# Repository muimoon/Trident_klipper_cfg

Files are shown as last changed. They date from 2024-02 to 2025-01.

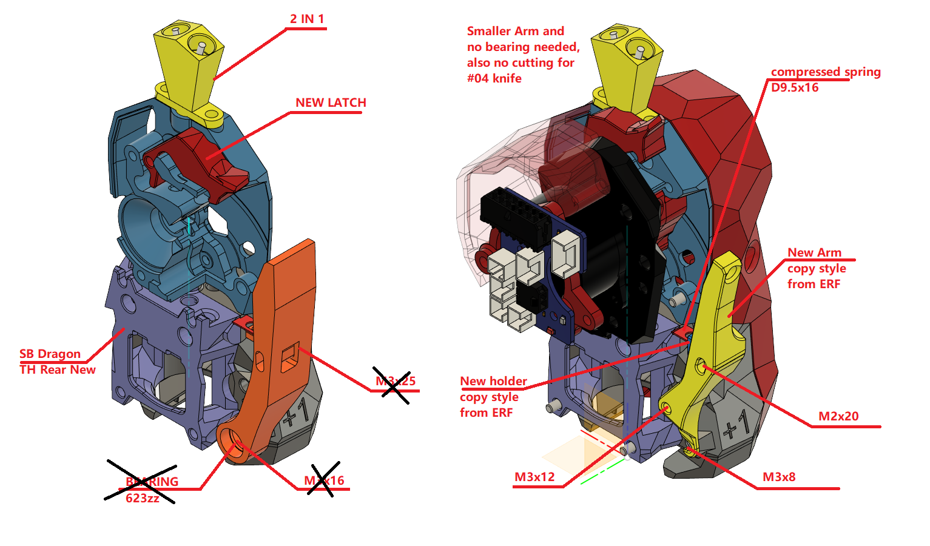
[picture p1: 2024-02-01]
fix knife Miu version BOM.png

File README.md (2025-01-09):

# Trident_klipper_cfg
Project combine two printer in one. 
The one is Voron Trident structure with ramp 1.6 (Mega2560) main board
The other one is Ender3 with MKS sgen L V2.0 board

Octopi and Klipper installed. 

printer.cfg included
 
https://clashforandroid.org/clash-for-android-download/
https://github.com/Clon1998/mobileraker/releases/tag/android2.8.4

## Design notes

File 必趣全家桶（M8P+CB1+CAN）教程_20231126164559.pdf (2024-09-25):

小恐龙交流群：786115036

# 必趣全家桶 M8P+CB1+CAN 教程

目录

# 恐龙 恐龙恐龙恐龙 恐龙恐龙恐龙 恐龙恐龙 恐龙恐龙恐龙 恐龙恐龙恐龙

## 1、系统准备

### 1.1 镜像系统烧录

烧录之前准备一张 8G 以上内存卡（推荐金士顿 32G）和读卡器。
进入 BIGTREETCH 的 GitHub 下载最新的 CB1 的系统镜像，推荐直接下载完整版。
地址：https://github.com/bigtreetech/CB1/releases

如果下载太慢就右键复制链接地址，再进入下面任意一个加速网站进行下载：
https://ghproxy.com/
https://github.ur1.fun/
下载完成后解压到自己找得到的地方

接着使用树莓派烧录软件进行镜像烧录
树莓派烧录器下载地址：https://www.raspberrypi.com/software/烧录之前可以用烧录器自带的擦除功能格式化一下内存卡，格式化完毕从新拔插一次内存卡。

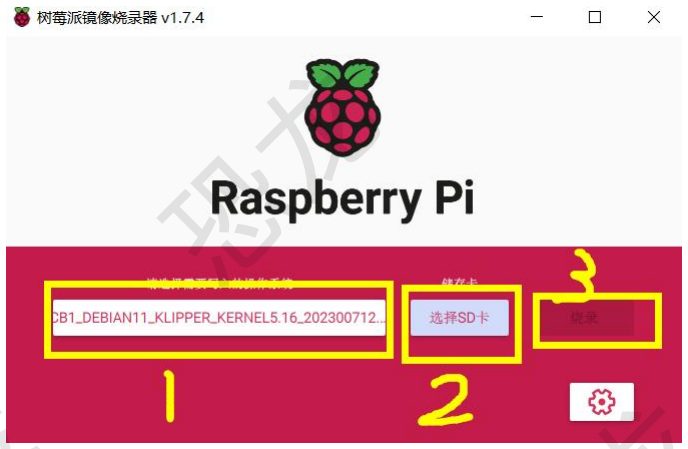
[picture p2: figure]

烧录完毕后重新拔插一次内存卡，用记事本（.txt）格式打开 boot 盘里面的 system.cfg 文件

# 恐龙 恐龙恐龙恐龙 恐龙恐龙恐龙 恐龙恐龙 恐龙恐龙恐龙 恐龙恐龙恐龙

找到 wifi 相关的内容，修改引号内的内容为自己的 wifi 账号和密码，注意不要删除引号！

改完以后一定要保存再关闭！

拔下内存卡插到 M8P 的 SOC Card 插口，即 CB1 天线模块下方的那个。不要插错，M8P 有两个内存卡插口。 另外，CB1 的天线需要插上，不插上搜不到 wifi！有条件的可以换个好点的 2.4G 天线，附带的天线有点拉跨。

# 恐龙 恐龙恐龙恐龙 恐龙恐龙恐龙 恐龙恐龙 恐龙恐龙恐龙 恐龙恐龙恐龙

## 1.2 ssh 连接上位机

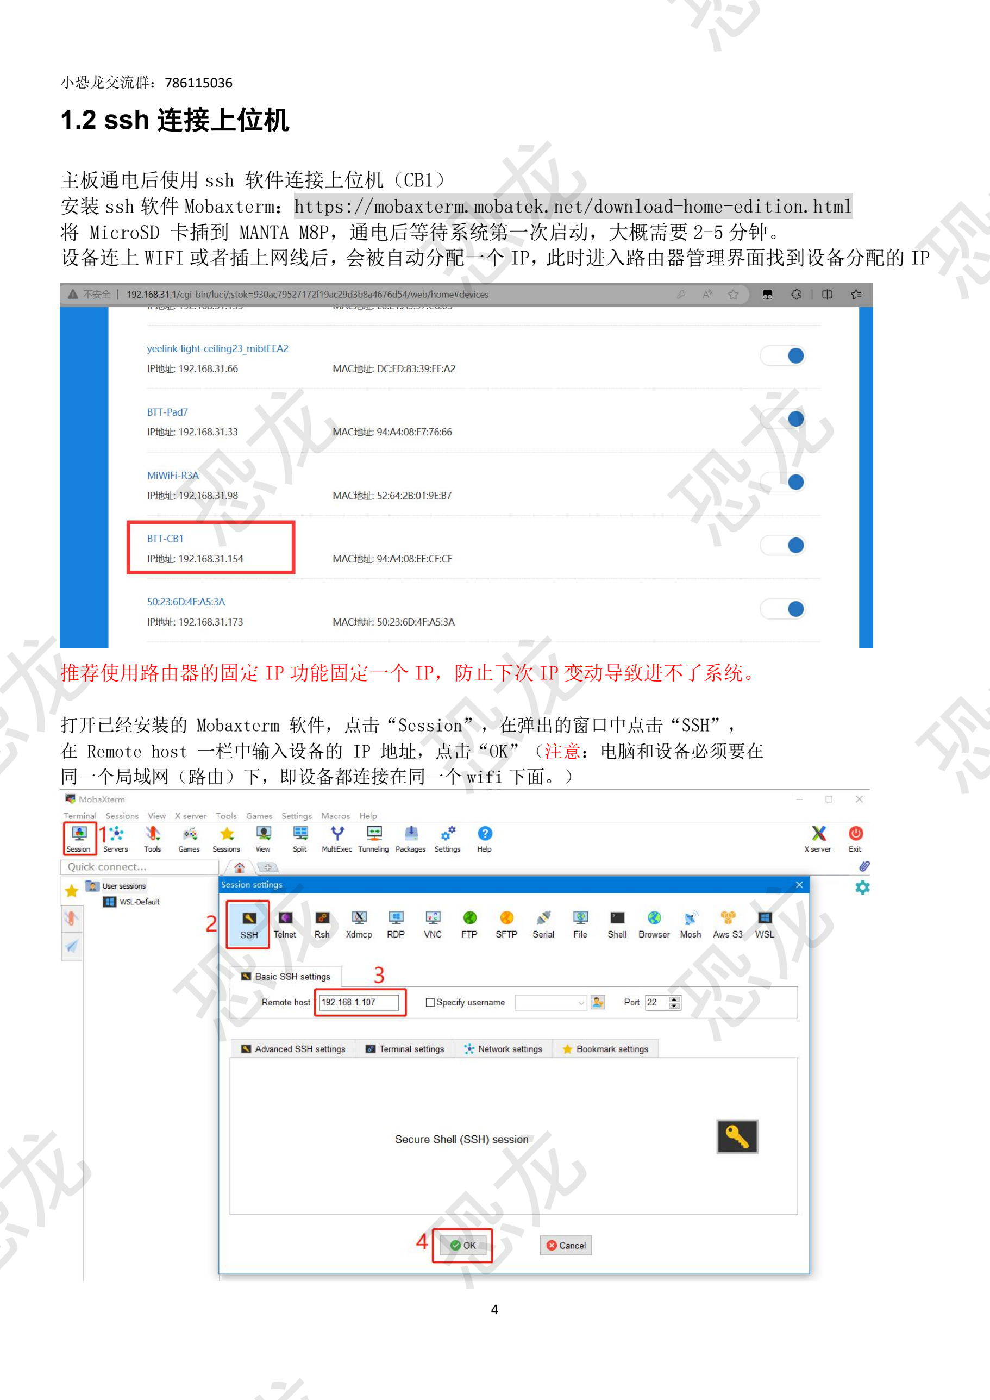
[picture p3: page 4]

主板通电后使用 ssh 软件连接上位机（CB1）
安装 ssh 软件 Mobaxterm：https://mobaxterm.mobatek.net/download-home-edition.html
将 MicroSD 卡插到 MANTA M8P，通电后等待系统第一次启动，大概需要 2-5 分钟。
设备连上 WIFI 或者插上网线后，会被自动分配一个 IP，此时进入路由器管理界面找到设备分配的 IP

推荐使用路由器的固定 IP 功能固定一个 IP，防止下次 IP 变动导致进不了系统。

打开已经安装的 Mobaxterm 软件，点击“Session”，在弹出的窗口中点击“SSH”， 在 Remote host 一栏中输入设备的 IP 地址，点击“OK”（注意：电脑和设备必须要在 同一个局域网（路由）下，即设备都连接在同一个 wifi 下面。）

# 恐龙 恐龙恐龙恐龙 恐龙恐龙恐龙 恐龙恐龙 恐龙恐龙恐龙 恐龙恐龙恐龙

输入登录名和登录密码进入 SSH 终端界面
登录名：biqu 密码：biqu（linux 系统输入密码不会显示内容，输完回车即可） 进入如下页面

# 恐龙 恐龙恐龙恐龙 恐龙恐龙恐龙 恐龙恐龙 恐龙恐龙恐龙 恐龙恐龙恐龙

## 2.主板固件烧录（不使用 Can 板）

## 2.1 编译主板 klipper 固件

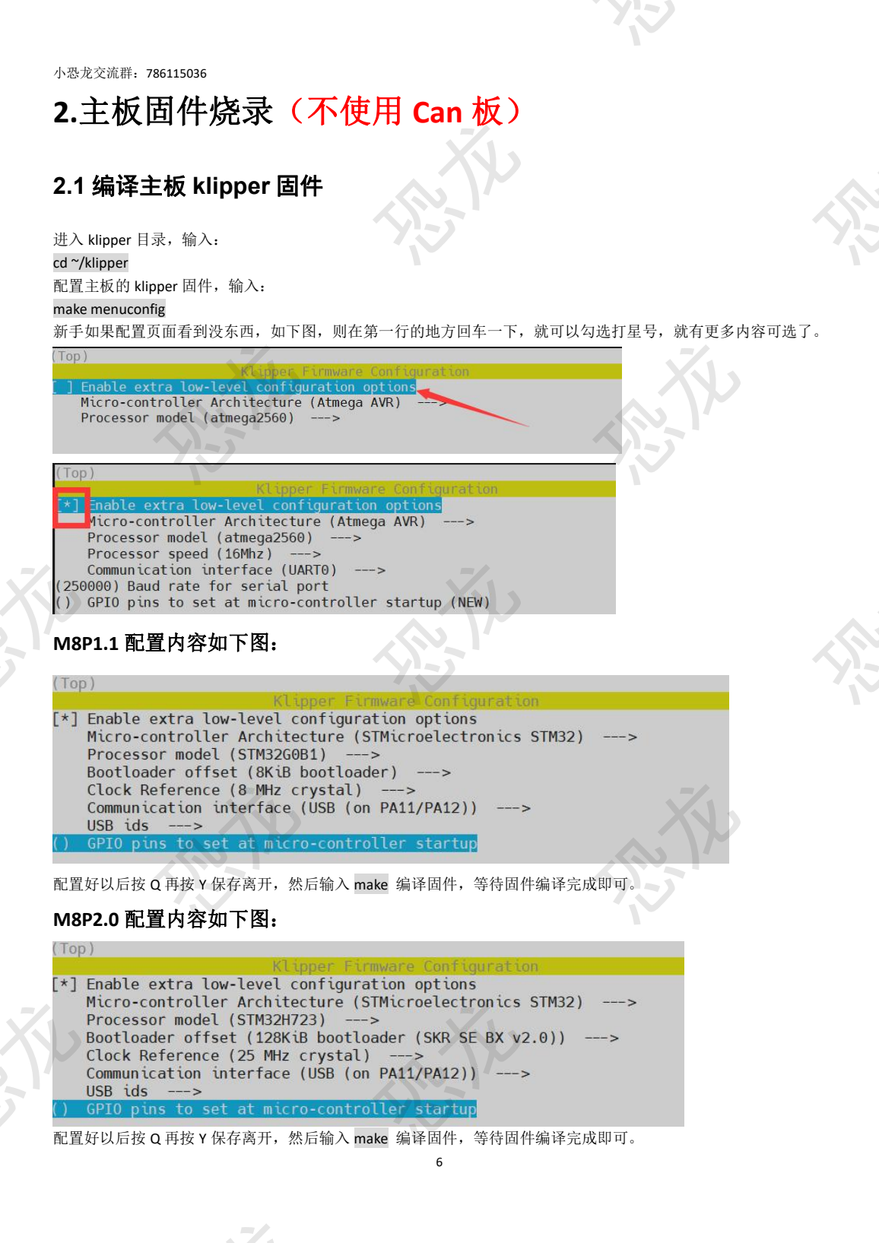
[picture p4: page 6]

进入 klipper 目录，输入：
cd ~/klipper
配置主板的 klipper 固件，输入：
make menuconfig
新手如果配置页面看到没东西，如下图，则在第一行的地方回车一下，就可以勾选打星号，就有更多内容可选了。

M8P1.1 配置内容如下图：

配置好以后按 Q 再按 Y 保存离开，然后输入 make | 编译固件，等待固件编译完成即可。 M8P2.0 配置内容如下图：
配置好以后按 Q 再按 Y 保存离开，然后输入 make | 编译固件，等待固件编译完成即可。

# 恐龙 恐龙恐龙恐龙 恐龙恐龙恐龙 恐龙恐龙 恐龙恐龙恐龙 恐龙恐龙恐龙

## 2.2 刷入 M8P 主板的 klipper 固件

首先主板进入 DFU 模式：
M8P1.1 主板就按住主板上的 BOOT 键不松，再按下 RESET 键，然后同时松开。 M8P2.0 主板就按住主板上的 BOOT0 键不松，再按下 RESET 键，然后同时松开。 按完后在再 ssh 输入 lsusb，如果出现如下图的信息则主板成功进入 DFU：

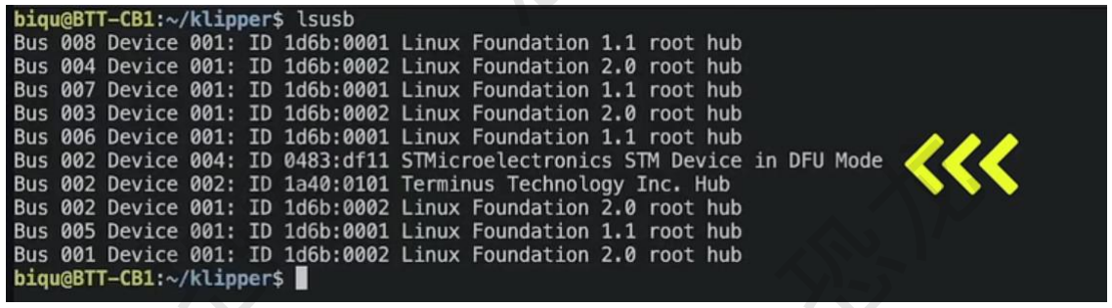
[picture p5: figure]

确认主板进入 dfu 模式后，进入 klipper 文件夹：
cd ~/klipper
接着输入下面命令输入 klipper 固件：
make flash FLASH_DEVICE=0483:df11
完成后按一下主板的 RESET 按键重启主板

## 2.3 读取 M8P 主板的 UUID

输入 ls /dev/serial/by-id/查询主板 uuid

复制读取到的 uuid 并填写到 printer.cfg 里面即可完成上位机和主板的通讯

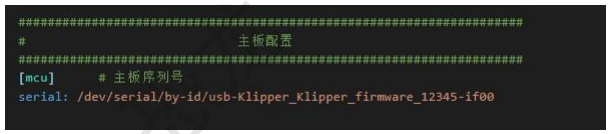
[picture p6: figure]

# | 主板配置

##################################################################### [mcu] # 主板序列号

serial: /dev/serial/by-id/Klipper_stm32h712xx_41003D001751303232383230-if00

# 恐龙 恐龙恐龙恐龙 恐龙恐龙恐龙 恐龙恐龙 恐龙恐龙恐龙 恐龙恐龙恐龙

## 3.主板固件烧录（使用 Can 板）

## 3.1 编译主板 katapult 固件即原 CanBoot 固件

首先下载 katapult（原 CanBoot），ssh 输入：
git clone https://github.com/Arksine/katapult
进入 katapult 目录，输入：
cd katapult
配置主板的 katapult 固件，输入：
make menuconfig
M8P1.1 配置内容如下图

注意：CAN bus speed 选项目前建议都设置为 1000000

配置好以后按 Q 再按 Y 保存离开，然后输入 make 编译固件，等待固件编译完成即可。 M8P2.0 配置内容如下如图

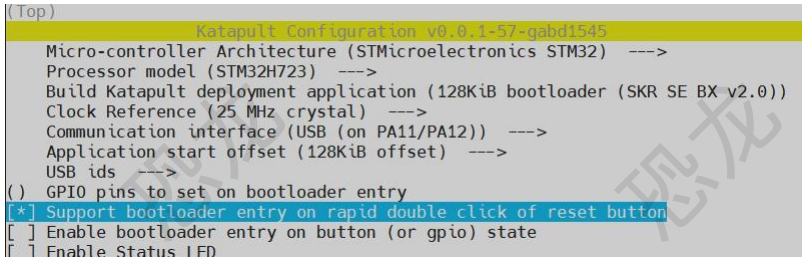
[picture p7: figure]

配置好以后按 Q 再按 Y 保存离开，然后输入 make 编译固件，等待固件编译完成即可。

## 3.2 编译主板的 klipper 固件

进入 klipper 目录，输入：
cd ~/klipper
配置主板的 klipper 固件，输入：
make menuconfig

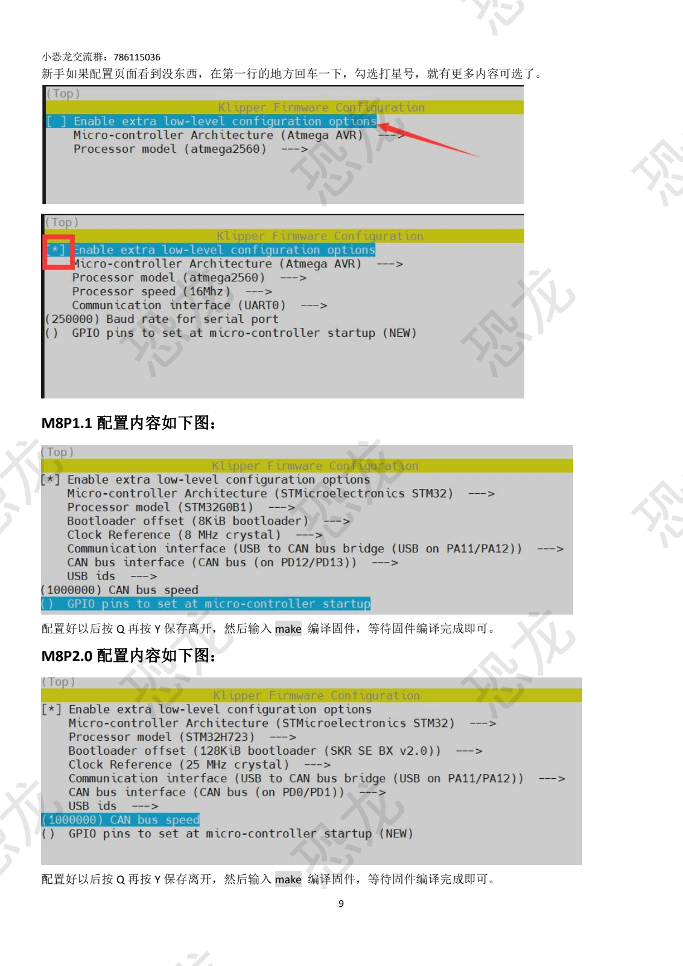
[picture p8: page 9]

新手如果配置页面看到没东西，在第一行的地方回车一下，勾选打星号，就有更多内容可选了。

M8P1.1 配置内容如下图：

配置好以后按 Q 再按 Y 保存离开，然后输入 make | 编译固件，等待固件编译完成即可。 M8P2.0 配置内容如下图：
配置好以后按 Q 再按 Y 保存离开，然后输入 make | 编译固件，等待固件编译完成即可。

# 恐龙 恐龙恐龙恐龙 恐龙恐龙恐龙 恐龙恐龙 恐龙恐龙恐龙 恐龙恐龙恐龙

## 3.3 刷入 M8P 主板的 katapult 和 klipper 固件

首先主板进入 DFU 模式：M8P1.1 主板就按住主板上的 boot 键不松，再按下 restart 键，然后同时松开。 M8P2.0 主板就按住主板上的 boot0 键不松，再按下 restart 键，然后同时松开。 按完后再 ssh 输入 lsusb，如果出现如下图的信息则主板成功进入 DFU：

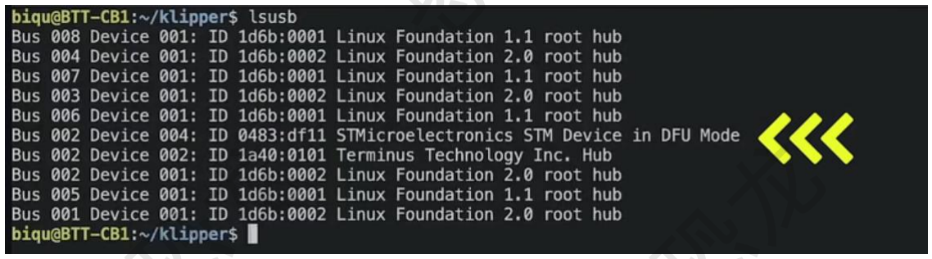
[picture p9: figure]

确认主板进入 dfu 模式后： M8P1.1 执行下面命令

首先输入下面命令刷写 katapult 固件：
sudo dfu-util -a 0 -D ~/katapult/out/katapult.bin --dfuse-address 0x08000000:force:mass-erase -d 0483:df11
上面命令刷写完成后，再输入下面命令刷写 klipper 固件：
sudo dfu-util -a 0 -d 0483:df11 --dfuse-address 0x08002000:force:leave -D ~/klipper/out/klipper.bin

## M8P2.0 执行下面命令

首先输入下面命令刷写 katapult 固件：
sudo dfu-util -a 0 -D ~/katapult/out/katapult.bin --dfuse-address 0x08000000:force:mass-erase -d 0483:df11
刷入成功后，按一下主板上的 RESET 按键重启主板
接着输入 ls /dev/serial/by-id/即可查询到主板的 UUID，如下图所示：

# 恐龙 恐龙恐龙恐龙 恐龙恐龙恐龙 恐龙恐龙 恐龙恐龙恐龙 恐龙恐龙恐龙

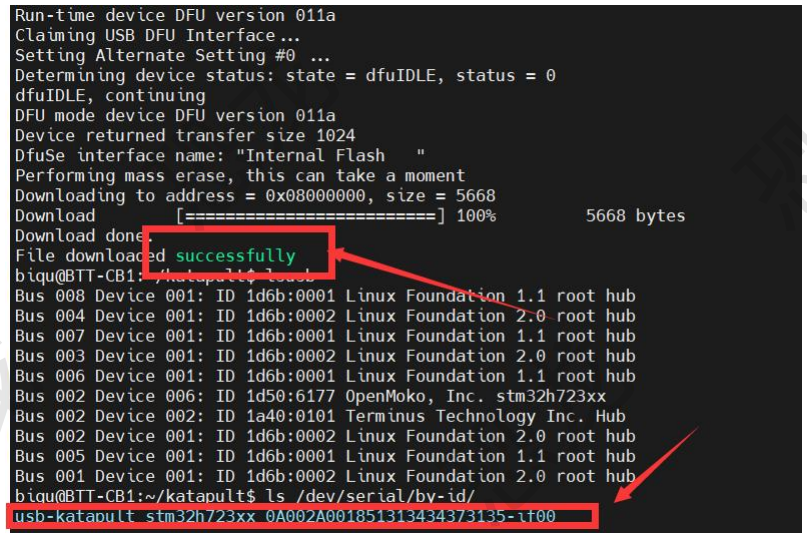
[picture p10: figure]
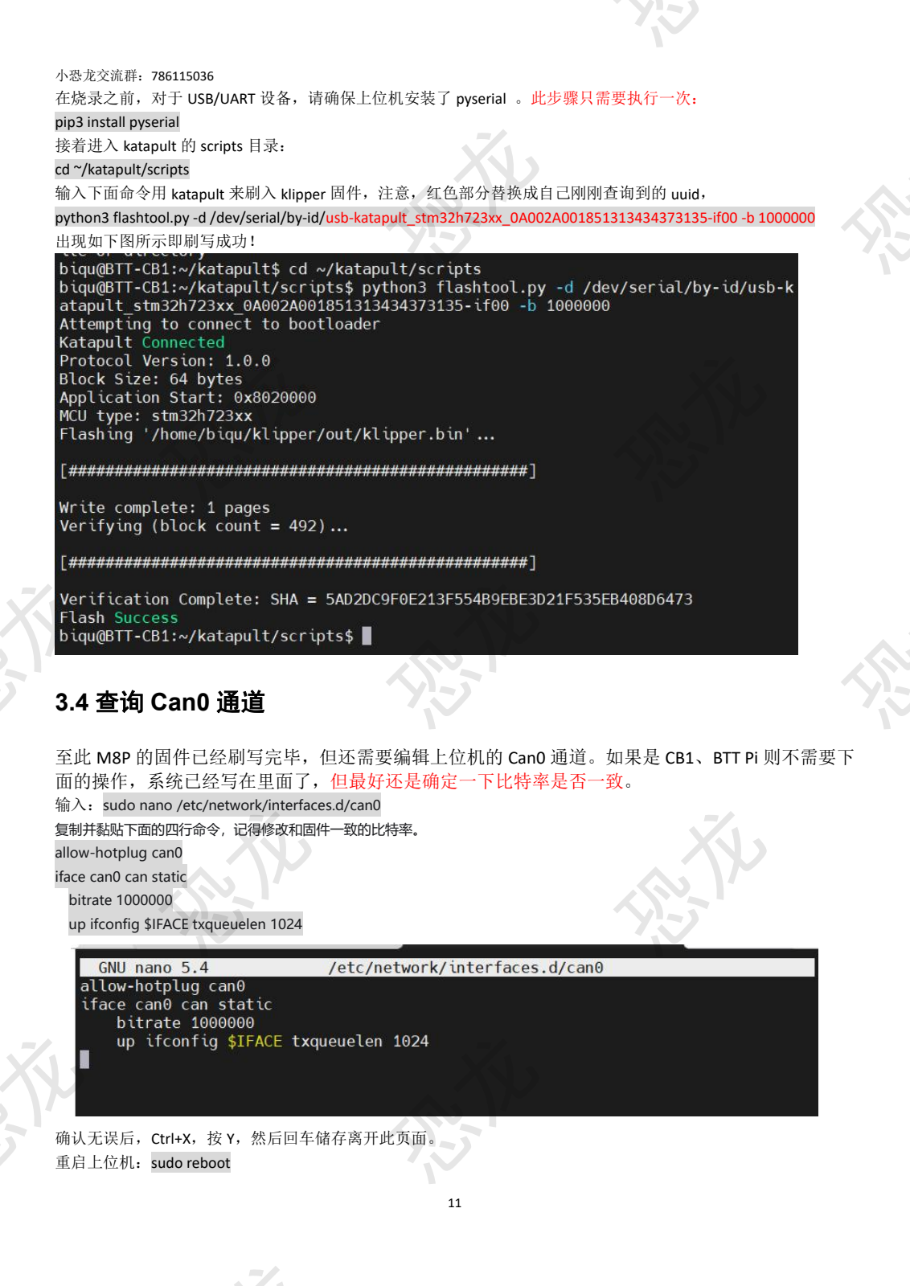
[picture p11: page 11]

在烧录之前，对于 USB/UART 设备，请确保上位机安装了 pyserial 。此步骤只需要执行一次：
pip3 install pyserial
接着进入 katapult 的 scripts 目录：
cd ~/katapult/scripts
输入下面命令用 katapult 来刷入 klipper 固件，注意，红色部分替换成自己刚刚查询到的 uuid，
python3 flashtool.py -d /dev/serial/by-id/usb-katapult_stm32h723xx_0A002A001851313434373135-if00 -b 1000000
出现如下图所示即刷写成功！

## 3.4 查询 Can0 通道

至此 M8P 的固件已经刷写完毕，但还需要编辑上位机的 Can0 通道。如果是 CB1、BTT Pi 则不需要下 面的操作，系统已经写在里面了，但最好还是确定一下比特率是否一致。
输入：sudo nano /etc/network/interfaces.d/can0
复制并黏贴下面的四行命令，记得修改和固件一致的比特率。
allow-hotplug can0
iface can0 can static
bitrate 1000000
up ifconfig $IFACE txqueuelen 1024

确认无误后，Ctrl+X，按 Y，然后回车储存离开此页面。
重启上位机：sudo reboot

# 恐龙 恐龙恐龙恐龙 恐龙恐龙恐龙 恐龙恐龙 恐龙恐龙恐龙 恐龙恐龙恐龙

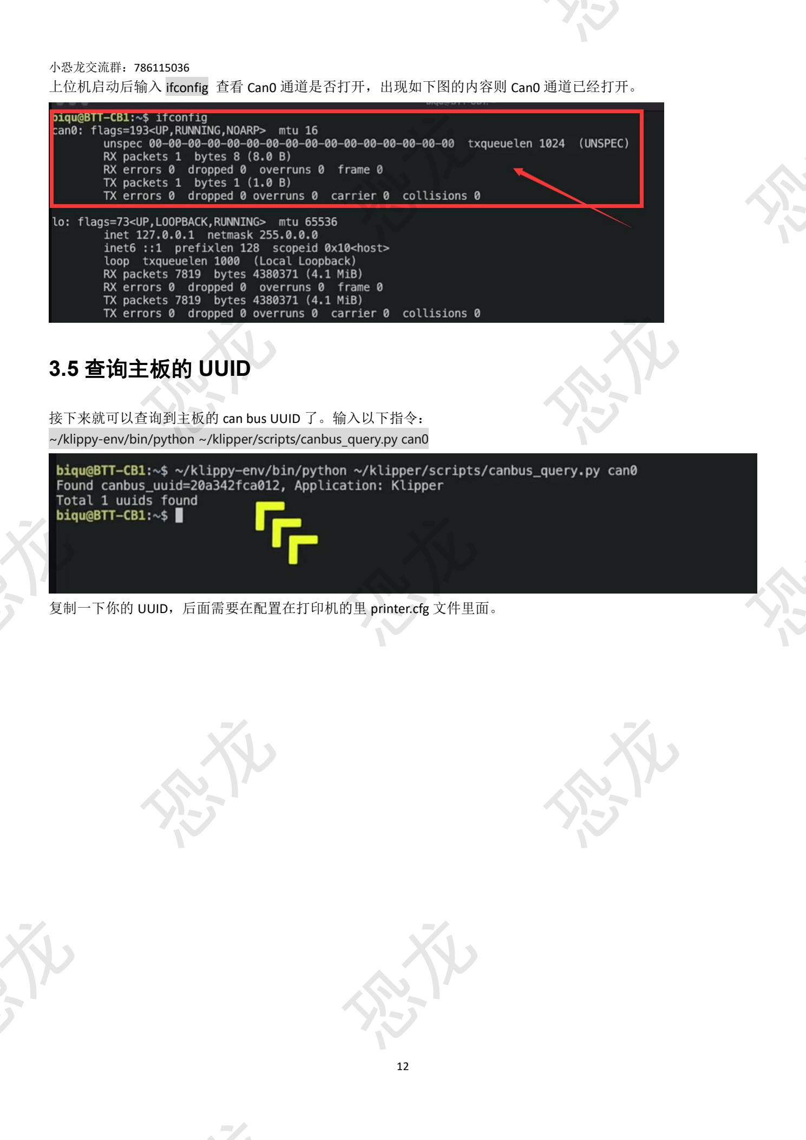
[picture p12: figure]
恐龙 恐龙恐龙恐龙 恐龙恐龙恐龙 恐龙恐龙 恐龙恐龙恐龙 恐龙恐龙恐龙

上位机启动后输入 ifconfig 查看 Can0 通道是否打开，出现如下图的内容则 Can0 通道已经打开。

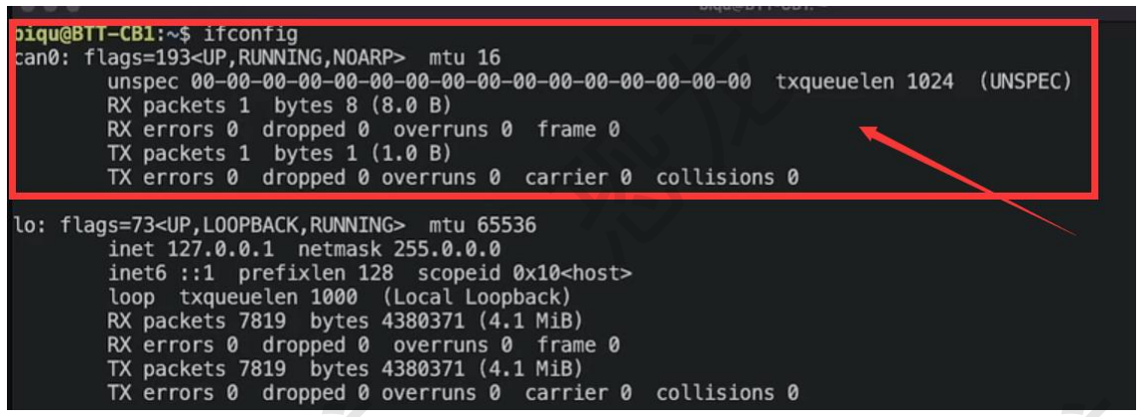
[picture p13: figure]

## 3.5 查询主板的 UUID

接下来就可以查询到主板的 can bus UUID 了。输入以下指令： ~/klippy-env/bin/python ~/klipper/scripts/canbus_query.py can0

复制一下你的 UUID，后面需要在配置在打印机的里 printer.cfg 文件里面。

# 4.刷写 Can 板固件

## 4.1 刷写 Can 板的 katapult 固件（原 CanBoot 固件）

进入 katapult 目录，输入：
cd katapult
配置主板的 katapult 固件，输入：
make menuconfig

## 使用 EBB SB2209/2240 如下图配置

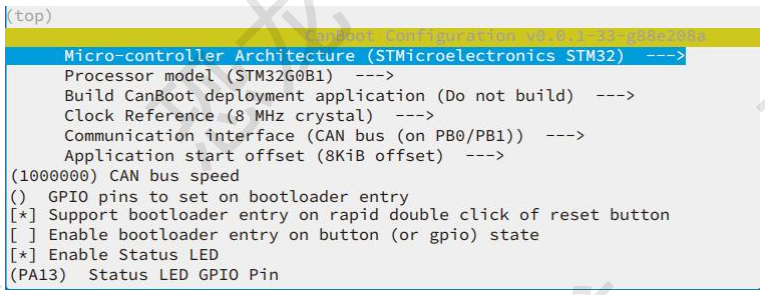
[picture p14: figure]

配置好以后按 Q 再按 Y 保存离开，然后输入 make | 编译固件，等待固件编译完成即可。 使用 EBB SB RP2040 如下图配置

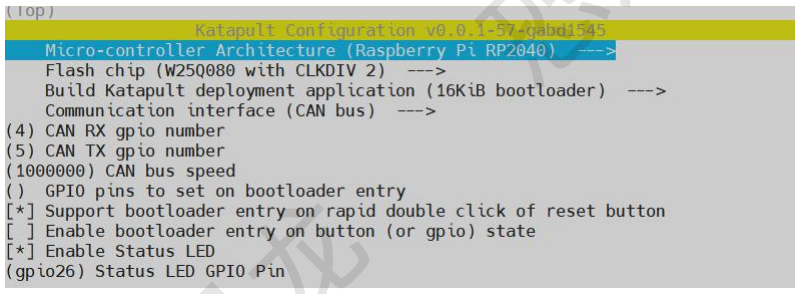
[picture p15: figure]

配置好以后按 Q 再按 Y 保存离开，然后输入 make | 编译固件，等待固件编译完成即可。 使用 EBB36/42 如下图配置

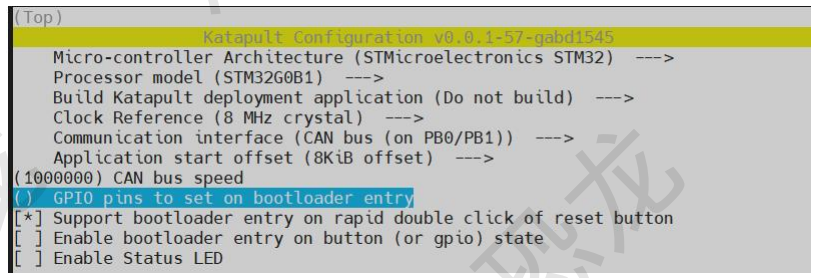
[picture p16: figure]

配置好以后按 Q 再按 Y 保存离开，然后输入 make 编译固件，等待固件编译完成即可。

# 恐龙 恐龙恐龙恐龙 恐龙恐龙恐龙 恐龙恐龙 恐龙恐龙恐龙 恐龙恐龙恐龙

### 4.2 连接 CAN 板和上位机

如未使用 24V 电源，则使用 Type-C 连接线将 EBB SB2209 CAN V1.0(RP2040) 或 EBB36/42 CAN 板连接至主板 USB 口 （上位机），并确保已连接 USB_5V 跳线帽，以便通过 Type-C 为 EBB SB2209 CAN (RP2040)或 EBB36Can 板提供电源。

EBB SB2209 CAN V1.0(RP2040)如下操作进入 DFU 模式：
按住 Boot 按钮，然后单击一下 Reset 按钮进入 DFU 模式。

使用 EBB36/42CAN 如下操作进入 DFU 模式：
按住 Boot 按钮，然后单击一下 Reset 按钮进入 DFU 模式。

## 4.3 给 Can 板烧录 katapult 固件

输入：lsusb

## EBB SB2209/2240 和 EBB36 如果出现如下图的信息则主板成功进入 DFU：

接着输入以下命令以烧录 katapult 固件：
sudo dfu-util -a 0 -d 0483:df11 -s 0x08000000:mass-erase:force -D ~/katapult/out/katapult.bin
其中“0483:df11”需替换为查询到的实际设备 ID

# 恐龙 恐龙恐龙恐龙 恐龙恐龙恐龙 恐龙恐龙 恐龙恐龙恐龙 恐龙恐龙恐龙

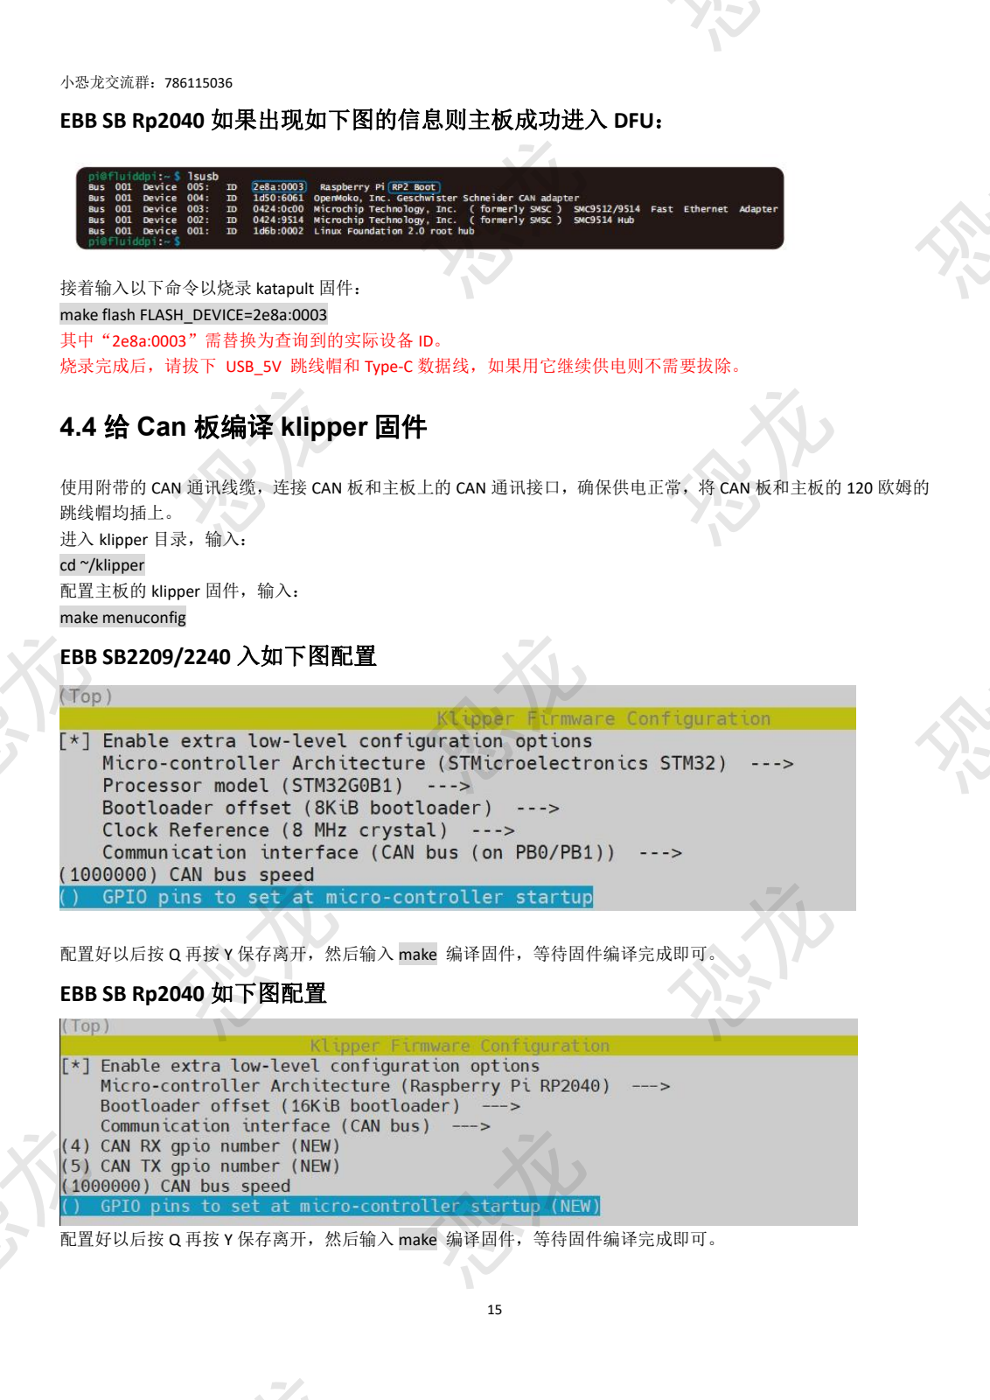
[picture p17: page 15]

EBB SB Rp2040 如果出现如下图的信息则主板成功进入 DFU：

接着输入以下命令以烧录 katapult 固件：
make flash FLASH_DEVICE=2e8a:0003
其中“2e8a:0003”需替换为查询到的实际设备 ID。
烧录完成后，请拔下 USB_5V 跳线帽和 Type-C 数据线，如果用它继续供电则不需要拔除。

## 4.4 给 Can 板编译 klipper 固件

使用附带的 CAN 通讯线缆，连接 CAN 板和主板上的 CAN 通讯接口，确保供电正常，将 CAN 板和主板的 120 欧姆的 跳线帽均插上。
进入 klipper 目录，输入：
cd ~/klipper
配置主板的 klipper 固件，输入：
make menuconfig

## EBB SB2209/2240 入如下图配置

配置好以后按 Q 再按 Y 保存离开，然后输入 make 编译固件，等待固件编译完成即可。

## EBB SB Rp2040 如下图配置

配置好以后按 Q 再按 Y 保存离开，然后输入 make 编译固件，等待固件编译完成即可。

# 恐龙 恐龙恐龙恐龙 恐龙恐龙恐龙 恐龙恐龙 恐龙恐龙恐龙 恐龙恐龙恐龙

## EBB36/42 如下图配置

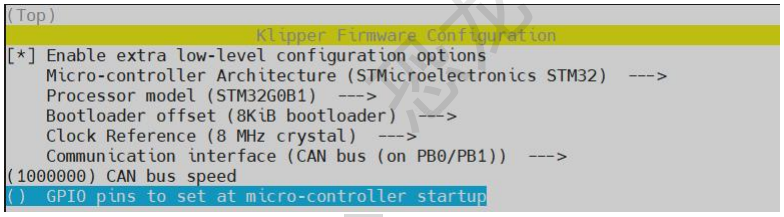
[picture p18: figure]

配置好以后按 Q 再按 Y 保存离开，然后输入 make 编译固件，等待固件编译完成即可。

## 4.5 使用 katapult 固件来刷写 Can 板的 klipper 固件

先输入命令：cd ~/katapult/scripts
再输入查看设备 uuid 命令：python3 flash_can.py -i can0 -q

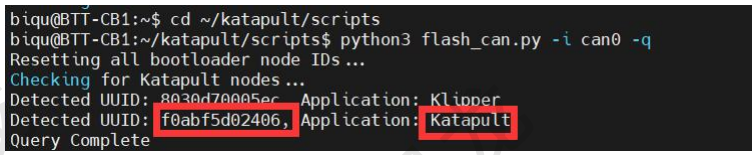
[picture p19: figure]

查询到 UUID 后，输入下面命令来烧录 klipper 固件，注意后面的 UUID 替换为实际的 UUID。
python3 flash_can.py -i can0 -f ~/klipper/out/klipper.bin -u be69315a613c
等待烧录完成后，再次输入下面命令查询固件状态，
python3 flash_can.py -i can0 -q

此时 Application 后面的 katapult 变为 Klipper，代表 Klipper 已经正常运行。

# 恐龙 恐龙恐龙恐龙 恐龙恐龙恐龙 恐龙恐龙 恐龙恐龙恐龙 恐龙恐龙恐龙

## 4.6 填写主板 uuid 和 can 板 uuid 进打印机配置

参考，记得替换自己的 uuid。

# | 主板配置

##################################################################### [mcu] # 主板序列号

#serial: /dev/serial/by-id/usb-Klipper_Klipper_firmware_12345-if00

canbus_uuid: 8c51c292b782

[mcu EBBCan]
# #serial: /dev/serial/by-id/usb-Klipper_Klipper_firmware_12345-if00

canbus_uuid: b9acf4c91547

### 填写完毕后保存并重启即可完成上位机和主板、CAN 板的通讯！

## 4.7 FLY 的 SHT36V2 Can 板刷 klipper

如使用 FLY 家的 SHT36 V2 CAN 板，则它已经自带 canboot 固件，只需要配置 klipper 固件即可。
将 36Can 通过通讯线连接到打印机主板并供电，确保接线正确！
进入 ssh 直接配置 SHT 36 V2 CAN 板的 klipper 固件即可
cd ~/klipper
make menuconfig
如下图配置即可：

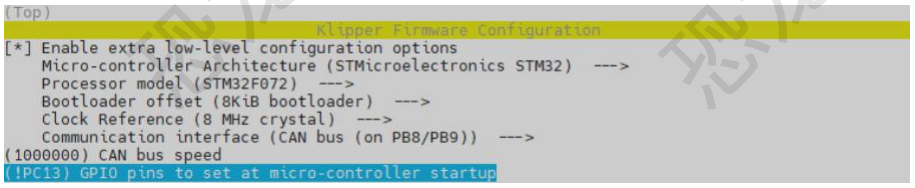
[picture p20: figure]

配置好以后按 Q 再按 Y 保存离开，然后输入 make 编译固件，等待固件编译完成。 接着烧录固件
cd ~/klipper
输入查询 Can 板 UUID 命令：
python3 ~/klipper/lib/canboot/flash_can.py -q
接着输入下面的命令烧录 klipper 固件，注意后面的 UUID 替换为实际的 UUID。
python3 lib/canboot/flash_can.py -i can0 -f ./out/klipper.bin -u fea6a45462e9

# 恐龙 恐龙恐龙恐龙 恐龙恐龙恐龙 恐龙恐龙 恐龙恐龙恐龙 恐龙恐龙恐龙

# 5.0 katapult（原 CanBoot）使用指南（未完成）

## 5.1 什么是 katapult？

Katapult 是一种为 ARM Cortex-M mcu 设计的引导加载程序。这个引导加载程序最初是为 CAN 节点设计的，以 便与 Klipper 一起使用。引导加载程序本身利用了 Klipper 的硬件抽象层，将内存占用最小化。除了 CAN, katapult 现
在还支持 USB 和 UART 接口。目前支持 lpc176x、stm32 和 rp2040 三种 mcu。CAN 支持目前仅限于 stm32 f 系列和 rp2040
设备。
Klipper 已支持 katapult，通过 CANBUS 直接烧录固件。使用 katapult 后为主板和 Can 通讯设备更新 klipper 固件
就无需再连接 USB 线，保持现有的 CAN 连接的情况下可直接烧录固件，能够更便捷、高效的更新 CAN 工具板的固 件。

## 5.2 更新 Klipper 固件

已经烧录过 Canboot 引导固件和带 Canboot 的固件，以后需要更新 klipper 固件看下面操作即可： 进入 klipper 目录，输入：
cd ~/klipper
拉取最新的 klipper 文件
git pull
编译最新的 klipper 固件
make clean
make menuconfig
继续按照文档中的 3.2 和 4.4 配置完后，输入 make 编译固件，等待固件编译完成
make -J4

对于 CAN 设备：

先输入下面命令查询 UUID
cd ~/katapult/scripts
python3 flash_can.py -i can0 -q
下面命令中的 fea6a45462e9 需要替换为你查询到的 UUID
python3 flash_can.py -i can0 -f ~/klipper/out/klipper.bin -u be69315a613c

对于 USB/UART 设备：阿巴阿巴阿巴阿吧

# 恐龙 恐龙恐龙恐龙 恐龙恐龙恐龙 恐龙恐龙 恐龙恐龙恐龙 恐龙恐龙恐龙

## 6.调机器教程

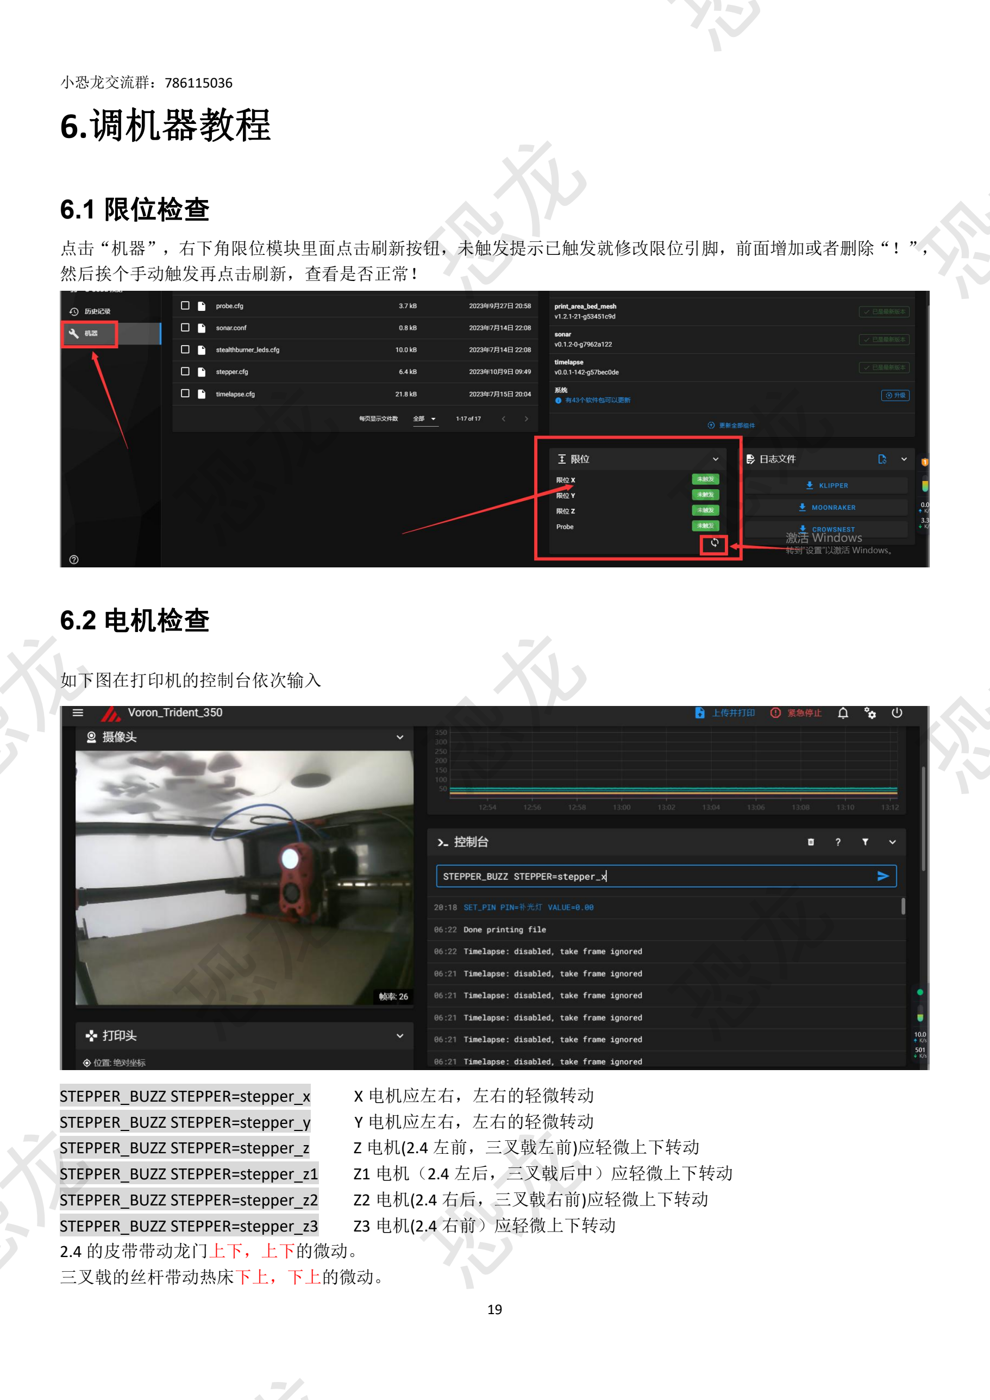
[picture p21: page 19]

### 6.1 限位检查

点击“机器”，右下角限位模块里面点击刷新按钮，未触发提示已触发就修改限位引脚，前面增加或者删除“！”， 然后挨个手动触发再点击刷新，查看是否正常！

### 6.2 电机检查

如下图在打印机的控制台依次输入

STEPPER_BUZZ STEPPER=stepper_x | X 电机应左右，左右的轻微转动
STEPPER_BUZZ STEPPER=stepper_y | Y 电机应左右，左右的轻微转动
STEPPER_BUZZ STEPPER=stepper_z | Z 电机(2.4 左前，三叉戟左前)应轻微上下转动
STEPPER_BUZZ STEPPER=stepper_z1 | Z1 电机（2.4 左后，三叉戟后中）应轻微上下转动
STEPPER_BUZZ STEPPER=stepper_z2 | Z2 电机(2.4 右后，三叉戟右前)应轻微上下转动
STEPPER_BUZZ STEPPER=stepper_z3 | Z3 电机(2.4 右前）应轻微上下转动
2.4 的皮带带动龙门上下，上下的微动。
三叉戟的丝杆带动热床下上，下上的微动。

# 恐龙 恐龙恐龙恐龙 恐龙恐龙恐龙 恐龙恐龙 恐龙恐龙恐龙 恐龙恐龙恐龙

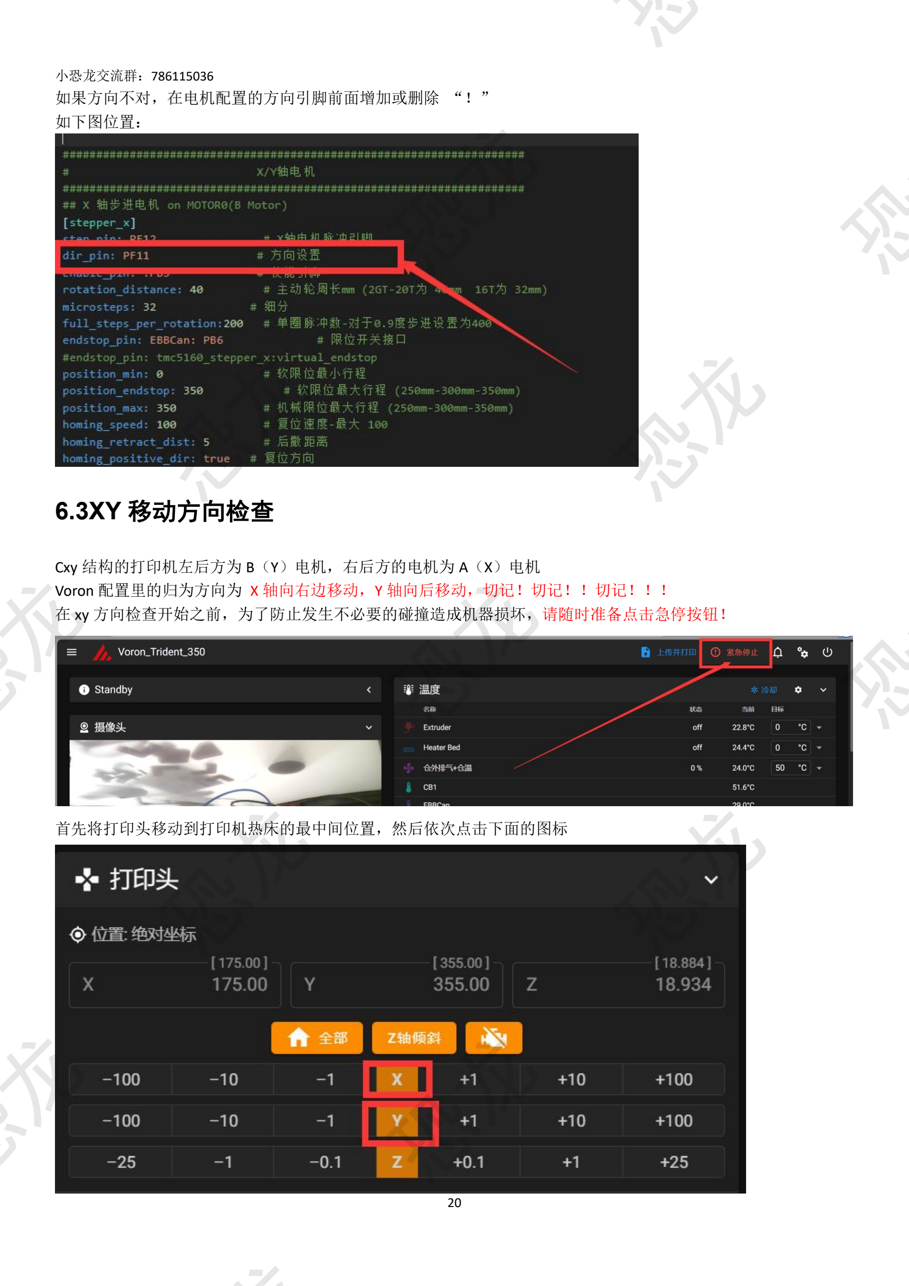
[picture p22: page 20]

如果方向不对，在电机配置的方向引脚前面增加或删除 “！” 如下图位置：

6.3XY 移动方向检查

Cxy 结构的打印机左后方为 B（Y）电机，右后方的电机为 A（X）电机
Voron 配置里的归为方向为 X 轴向右边移动，Y 轴向后移动，切记！切记！！切记！！！
在 xy 方向检查开始之前，为了防止发生不必要的碰撞造成机器损坏，请随时准备点击急停按钮！

首先将打印头移动到打印机热床的最中间位置，然后依次点击下面的图标

# 恐龙 恐龙恐龙恐龙 恐龙恐龙恐龙 恐龙恐龙 恐龙恐龙恐龙 恐龙恐龙恐龙

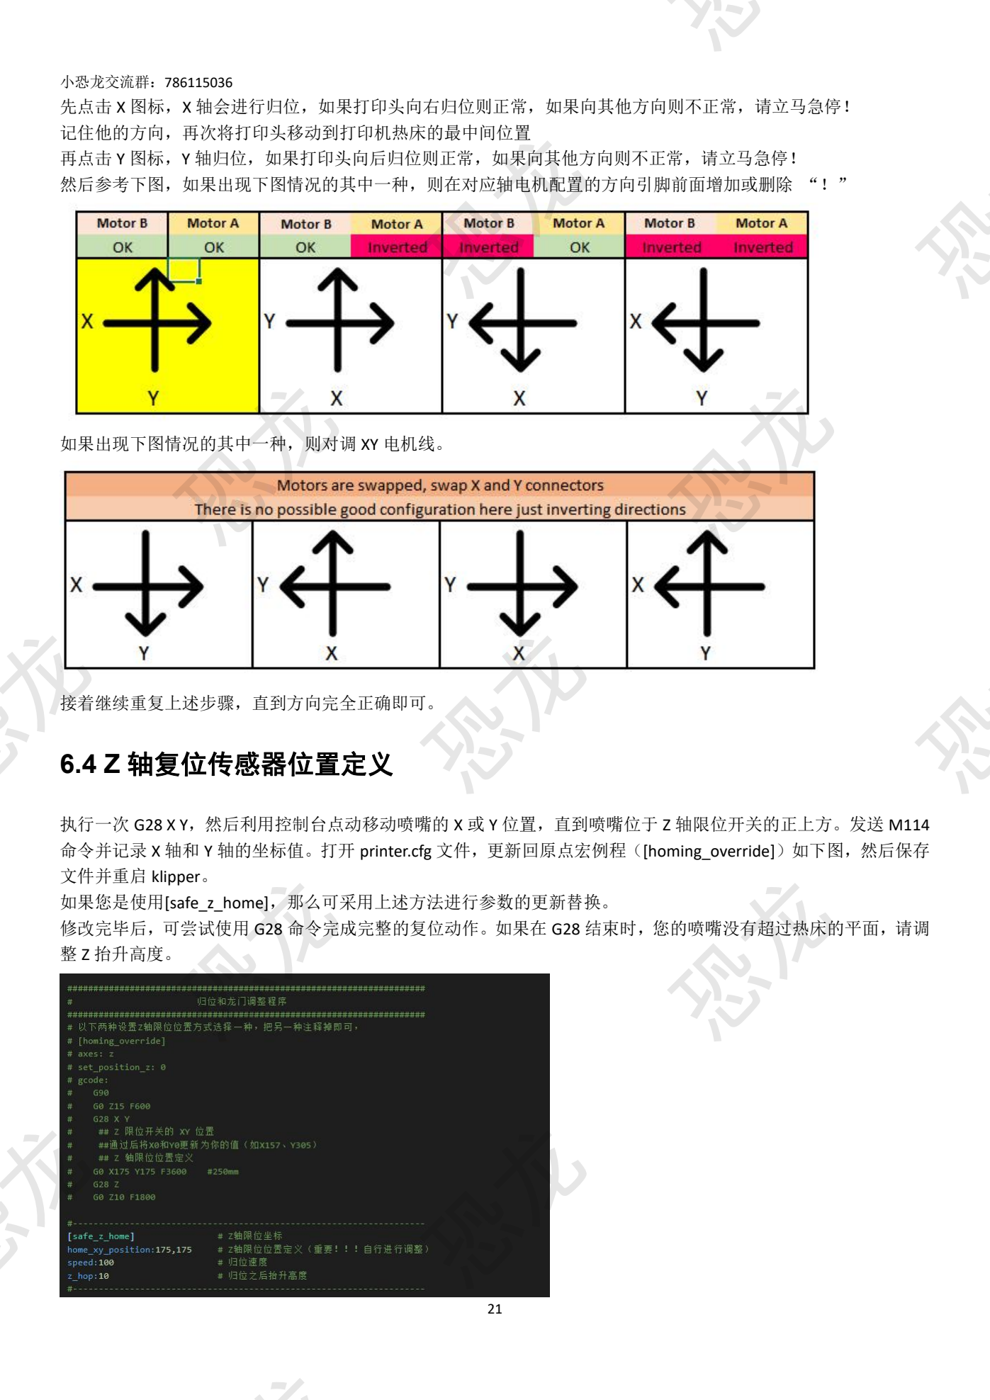
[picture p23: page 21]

先点击 X 图标，X 轴会进行归位，如果打印头向右归位则正常，如果向其他方向则不正常，请立马急停！ 记住他的方向，再次将打印头移动到打印机热床的最中间位置
再点击 Y 图标，Y 轴归位，如果打印头向后归位则正常，如果向其他方向则不正常，请立马急停！ 然后参考下图，如果出现下图情况的其中一种，则在对应轴电机配置的方向引脚前面增加或删除 “！”

如果出现下图情况的其中一种，则对调 XY 电机线。

接着继续重复上述步骤，直到方向完全正确即可。

### 6.4 Z 轴复位传感器位置定义

执行一次 G28 X Y，然后利用控制台点动移动喷嘴的 X 或 Y 位置，直到喷嘴位于 Z 轴限位开关的正上方。发送 M114 命令并记录 X 轴和 Y 轴的坐标值。打开 printer.cfg 文件，更新回原点宏例程（[homing_override]）如下图，然后保存
文件并重启 klipper。
如果您是使用[safe_z_home]，那么可采用上述方法进行参数的更新替换。
修改完毕后，可尝试使用 G28 命令完成完整的复位动作。如果在 G28 结束时，您的喷嘴没有超过热床的平面，请调 整 Z 抬升高度。

# 恐龙 恐龙恐龙恐龙 恐龙恐龙恐龙 恐龙恐龙 恐龙恐龙恐龙 恐龙恐龙恐龙

## 6.5 加热器 PID 校准

1、热床 PID 校准命令如下
PID_CALIBRATE HEATER=heater_bed TARGET=100
2、加热棒 PID 校准命令如下，记得先打开模型散热风扇，风力调整到 25%。
PID_CALIBRATE HEATER=extruder TARGET=245

## 6.6 probe 传感器精度

首次测试 probe 传感器，不需要加热喷头和热床，G28 复位后将打印头移到热床的中心，然后发送命令：
PROBE_ACCURACY
此时喷头会自动下降直至 probe 传感器被触发后反向抬升，如此连续探测热床 10 次，并在最后输出一个标准偏差 值，标准偏差应小于 0.003mm。如果每次的探测值不稳定或者是呈趋势性的变化，需要检查 Z 轴皮带的松紧度。劣 质的传感器也会影响重复探测的精度。

### 6.7 龙门调平（或 Z 倾斜）

在进行 4Z 调平操作之前，先打开 printer.cfg 配置文件，找到 4Z 调平的宏[quad_gantry_level]，根据热床大小调整 4
个探测点的坐标位置，确保探测点都在热床打印区域以内。
第一次运行 4Z 调平前，请先用手将龙门的 4 个角高度调至差不多一致，先运行一次 G28 归位，然后发送命令：
Voron2.4 发送：Quad_Gantry_Level
三叉戟发送：Z_Tilt
打印机开始执行自动调平动作，喷头从左前角开始采集高度数据，并按逆时针依次探测完 4 个点。每次探测完，系 统会自动计算出一个平均的公差值，并自动调整 4 个角的高度。重复探测 2-3 次，直至公差值小于 retry_tolerance: 的 设定值，即完成了 4Z 调平的动作。
注意：果偏差越来越大，请检查是电机的顺序是否正确。如果探测次数超过 5 圈仍未达到预设公差，系统将会报错。 Z 轴皮带的松紧程度以及劣质的传感器都会影响重复探测的精度

### 6.8 挤出机校准

在第一次打印之前，需要确保挤出机能挤出正确长度的材料。根据打印材料所需的温度，加热挤出头，从挤出机进 料口的铁氟龙管口处量 150mm 料丝，并在 100mm 处用美工刀做一个标记。在网页中，手动操作挤出 50mm2 次， 共 100mm（Klipper 的单次挤出量不允许超过 50mm）。待挤出机停止后，测量从挤出机进料口到标记处的长度 x。 如果挤出量正确的时候，x 应该为 50mm（150mm - 100mm =50mm）。但实际是会有偏差的，找到配置文件中的现 有挤出值，并使用以下方法更新它。

# 恐龙 恐龙恐龙恐龙 恐龙恐龙恐龙 恐龙恐龙 恐龙恐龙恐龙 恐龙恐龙恐龙

新收缩值=旧收缩值×（实际挤出量÷目标挤出量）

将新值替换配置文件中，保存并重启 klipper。然后按上述方法重新再验证一遍，如果挤出量在目标值的±0.5%范围 内（即，目标值为 99.5-100.5mm，目标挤出长度为 100mm），挤出机就校准好了。

### 6.9 Z 复位偏移调整

对 Z 复位偏移的调整，其实就是是调整 Z 轴在高度为 0 时，喷嘴距热床的高度，他关系到打印时，首层的高度是否 正确，料丝是否能良好的粘附在热床上。在做此项操作前，请将挤出机设置为 240℃，热床加热至 100℃，预热 15 分钟后开
始以下操作。
1、先执行一次 G32 。
2、然后将打印头移至热床中心，运行命令
Z_ENDSTOP_CALIBRATE
然后使用命令 TESTZ Z=-1 缓慢地将喷头移向热床表面，直到喷头离热床表面约 1mm 时，在热床与喷嘴之间垫一 张 A4 白纸，然后使用微调指令 TESTZ Z=-0.1 使喷嘴慢慢接近热床表面，直至喷嘴接接触到 A4 纸，用手抽拉白纸有 轻微阻力，此时可执行确认命令 ACCEPT ，然后执行保存命令 SAVE_CONFIG ，将自动把参数保存到配置文件中。 在上述调试过程中，如果喷头下降的太多，导致 A4 纸抽拉不动，可使用正数 TESTZ Z=0.1 ，使喷嘴抬高。 重要：在保存完参数后，马上执行 G28 复位，使喷头离开热床表面，以免烫坏 PEI 膜。 如果在执行过程中出现报错(越界)，一般是由于 Z 限位传感器的的轴太长，可能会在打印过程中卡住打印头。最好 切割轴，使其与 PEI 的表面平齐。

### 6.10 动态微调 Z 轴高度

由于 A4 纸大法并不能完美首层高度，所以打印过程中，可以使用工具面板上的 Z 偏移微调按钮来动态调整喷嘴的 高度。

调整完成如果希望系统一直使用当前高度，直接点击保存即可。

# 恐龙 恐龙恐龙恐龙 恐龙恐龙恐龙 恐龙恐龙 恐龙恐龙恐龙 恐龙恐龙恐龙

### 6.11 加速度计的使用

如果使用了带加速度计 CAN 板，则可以直接使用，参考 Can 板引脚配置好加速度计后，如果是 CB1 上位机直接输 入下面的命令即可。
SHAPER_CALIBRATE
测试完成后直接点击保存即可。

如果不是 CB1 上位机则需要安装科学依赖库
1.安装 Python 的科学计算库
~/klippy-env/bin/pip install -v numpy
2.安装系统依赖库
sudo apt install python-numpy python-matplotlib
sudo 指令需要输入用户的密码
3.查看 klipper 是否会正常运行
ACCELEROMETER_QUERY
4.输入代码开始自动测试打印机震动
SHAPER_CALIBRATE
5.保存
SAVE_CONFIG

### 6.12 摄像头配置

CB1 系统镜像已经配置好摄像头，只需要插上 USB 免驱摄像头再按照下图添加即可，如图

# 恐龙 恐龙恐龙恐龙 恐龙恐龙恐龙 恐龙恐龙 恐龙恐龙恐龙 恐龙恐龙恐龙

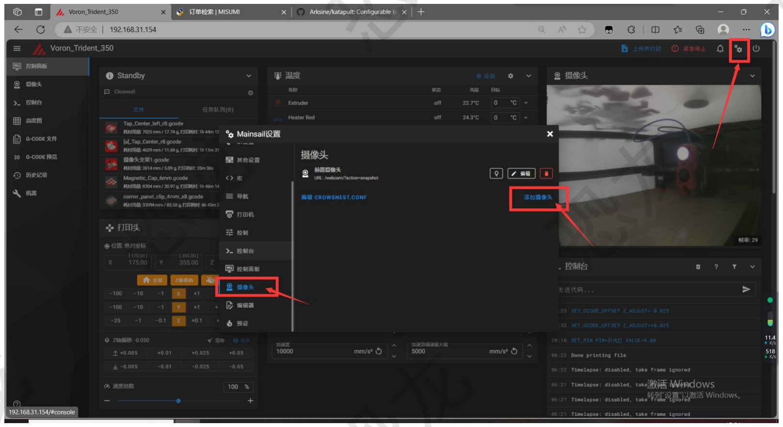
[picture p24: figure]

## 6.13 添加 KlipperScreen 屏幕

## 6.14 必趣 SFS2.0 智能断料传感器

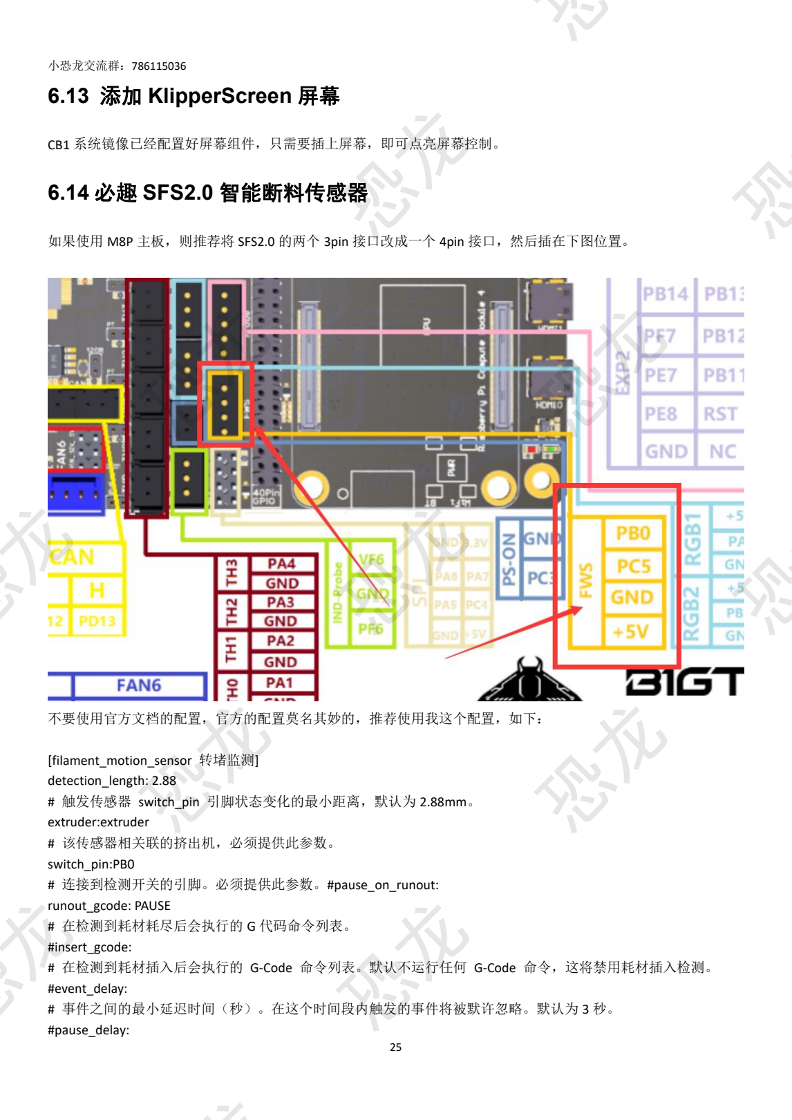
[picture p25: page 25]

CB1 系统镜像已经配置好屏幕组件，只需要插上屏幕，即可点亮屏幕控制。

如果使用 M8P 主板，则推荐将 SFS2.0 的两个 3pin 接口改成一个 4pin 接口，然后插在下图位置。

不要使用官方文档的配置，官方的配置莫名其妙的，推荐使用我这个配置，如下：

[filament_motion_sensor 转堵监测]
detection_length: 2.88
# 触发传感器 switch_pin 引脚状态变化的最小距离，默认为 2.88mm。

extruder:extruder
# 该传感器相关联的挤出机，必须提供此参数。

switch_pin:PB0
# 连接到检测开关的引脚。必须提供此参数。#pause_on_runout:

runout_gcode: PAUSE
# 在检测到耗材耗尽后会执行的 G 代码命令列表。

#insert_gcode:

# 在检测到耗材插入后会执行的 G-Code 命令列表。默认不运行任何 G-Code 命令，这将禁用耗材插入检测。

#event_delay:

# 事件之间的最小延迟时间（秒）。在这个时间段内触发的事件将被默许忽略。默认为 3 秒。

#pause_delay:

# 恐龙 恐龙恐龙恐龙 恐龙恐龙恐龙 恐龙恐龙 恐龙恐龙恐龙 恐龙恐龙恐龙

# 暂停命令和执行 runout_gcode 之间的延迟时间, 单位是秒。如果在 OctoPrint 的情况下，增加这个延迟可能改善 暂停的可靠性。如果 OctoPrint 表现出奇怪的暂停行为，考虑增加这个延迟。默认为 0.5 秒。

[filament_switch_sensor 断料监测]。
pause_on_runout: True
# 当设置为 "True "时，会在检测到耗尽后立即暂停打印机。请注意, 如果 pause_on_runout 为 False 并且没有定 义。runout_gcode 的话, 耗尽检测将被禁用。默认为 True。

runout_gcode: PAUSE
# 在检测到耗材耗尽后会执行的 G 代码命令列表。如果 pause_on_runout 被设置为 True，这个 G-Code 将在暂停后 执行。默认情况是不运行任何 G-Code 命令。

# insert_gcode:

# 在检测到耗材插入后会执行的 G-Code 命令列表。默认不运行任何 G-Code 命令，这将禁用耗材插入检测。

event_delay: 3.0
# 事件之间的最小延迟时间（秒）。在这个时间段内触发的事件将被默许忽略。默认为 3 秒。

pause_delay: 0.5
# 暂停命令和执行 runout_gcode 之间的延迟时间, 单位是秒。如果在 OctoPrint 的情况下，增加这个延迟可能改善 暂停的可靠性。如果 OctoPrint 表现出奇怪的暂停行为，考虑增加这个延迟。默认为 0.5 秒。

switch_pin:PC5
# 连接到检测开关的引脚。必须提供此参数。

# 恐龙 恐龙恐龙恐龙 恐龙恐龙恐龙 恐龙恐龙 恐龙恐龙恐龙 恐龙恐龙恐龙

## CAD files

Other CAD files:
Muzi_ams.dwg
filament_buffer.dwg

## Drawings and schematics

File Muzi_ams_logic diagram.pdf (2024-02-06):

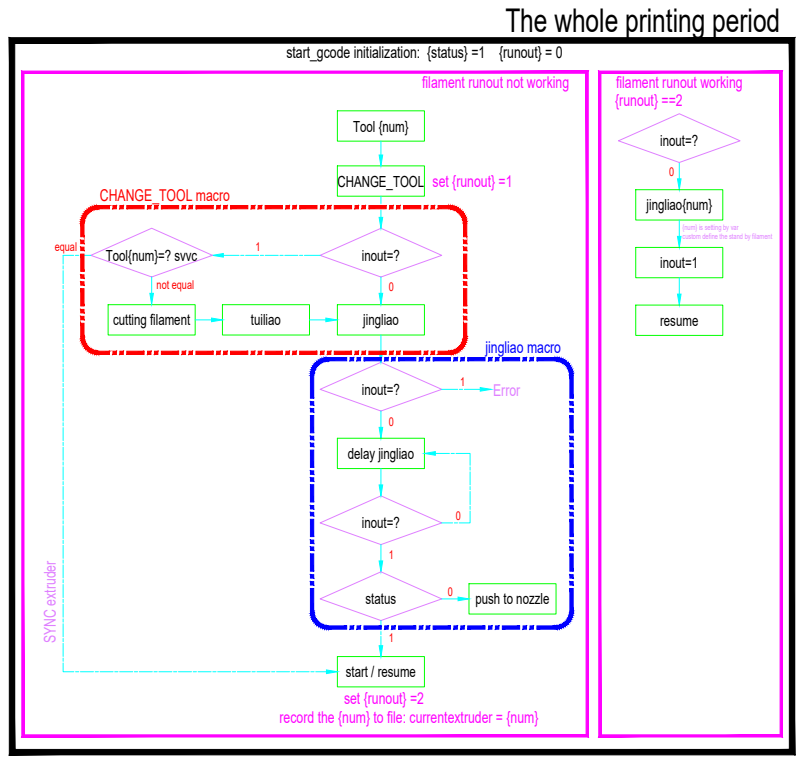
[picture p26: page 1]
Tool {num} CHANGE_TOOL inout=? 1; jingliao inout=? delay jingliao 0 inout=?1; Error Tool{num}=? svvc equal

SYNC extruder not equal cutting filament tuiliao 0 start / resume status1 0 push to nozzle jingliao macro CHANGE_TOOL macro filament runout not working filament runout working The whole printing period jingliao{num} {num} is setting by var custom define the stand by filament inout=1 inout=? 0 resume set {runout} =1 set {runout} =2 {runout} ==2 start_gcode initialization: {status} =1 {runout} = 0 record the {num} to file: currentextruder = {num}

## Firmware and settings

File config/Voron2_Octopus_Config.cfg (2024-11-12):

# This file contains common pin mappings for the BigTreeTech Octopus V1.
# To use this config, the firmware should be compiled for the STM32F446 with a "32KiB bootloader"
# Enable "extra low-level configuration options" and select the "12MHz crystal" as clock reference

# after running "make", copy the generated "klipper/out/klipper.bin" file to a
# file named "firmware.bin" on an SD card and then restart the OctoPus with that SD card.

# See docs/Config_Reference.md for a description of parameters.

## Voron Design VORON2 250/300/350mm BigTreeTech OctoPus V1 TMC2209 UART config

## *** THINGS TO CHANGE/CHECK: ***
## MCU paths                            [mcu] section
## Thermistor types                     [extruder] and [heater_bed] sections - See 'sensor types' list at end of file
## Z Endstop Switch location            [safe_z_home] section
## Homing end position                  [gcode_macro G32] section
## Z Endstop Switch  offset for Z0      [stepper_z] section
## Probe points                         [quad_gantry_level] section
## Min & Max gantry corner postions     [quad_gantry_level] section
## PID tune                             [extruder] and [heater_bed] sections
## Thermistor types                     [extruder] and [heater_bed] sections
## Probe pin                            [probe] section
## Fine tune E steps                    [extruder] section

[mcu]
##  Obtain definition by "ls -l /dev/serial/by-id/" then unplug to verify
##--------------------------------------------------------------------
#serial: /dev/serial/by-id/{REPLACE WITH YOUR SERIAL}
serial: /dev/serial/by-id/usb-Klipper_stm32f446xx_450053000451313133353932-if00
#restart_method: command
##--------------------------------------------------------------------

[printer]
kinematics: corexy
max_velocity: 300  
max_accel: 3000             #Max 4000
max_z_velocity: 15          #Max 15 for 12V TMC Drivers, can increase for 24V
max_z_accel: 300
square_corner_velocity: 5.0

[gcode_arcs]
resolution: 0.1

[exclude_object]

[gcode_macro PID_extruder]
gcode:
  PID_CALIBRATE HEATER=extruder TARGET=200

#####################################################################
#   X/Y Stepper Settings
#####################################################################

##  B Stepper - Left
##  Connected to MOTOR_0
##  Endstop connected to DIAG_0
[stepper_x]
step_pin: PF13
dir_pin: PF12
enable_pin: !PF14
rotation_distance: 40
microsteps: 16 #32
full_steps_per_rotation:200  #set to 400 for 0.9 degree stepper
endstop_pin: PG6
position_min: 0
##--------------------------------------------------------------------

##  Uncomment below for 250mm build
position_endstop: 250
position_max: 250

##  Uncomment for 300mm build
#position_endstop: 300
#position_max: 300

##  Uncomment for 350mm build
#position_endstop: 350
#position_max: 350

##--------------------------------------------------------------------
homing_speed: 80   #Max 100
homing_retract_dist: 5
homing_positive_dir: true

########################################
# tmc5160 configuration
########################################

[tmc5160 stepper_x]
cs_pin: PC4
run_current: 0.800
hold_current: 0.500
stealthchop_threshold: 0
spi_software_mosi_pin: PA7
spi_software_miso_pin: PA6
spi_software_sclk_pin: PA5

##  Make sure to update below for your relevant driver (2208 or 2209)
#[tmc2209 stepper_x]
#uart_pin: PC4
#interpolate: false
#run_current: 0.8
#sense_resistor: 0.110
#stealthchop_threshold: 0

##  A Stepper - Right
##  Connected to MOTOR_1
##  Endstop connected to DIAG_1
[stepper_y]
step_pin: PG0
dir_pin: PG1
enable_pin: !PF15
rotation_distance: 40
microsteps: 16
full_steps_per_rotation:200  #set to 400 for 0.9 degree stepper
endstop_pin: PG9
position_min: 0
##--------------------------------------------------------------------

##  Uncomment for 250mm build
position_endstop: 250
position_max: 250

##  Uncomment for 300mm build
#position_endstop: 300
#position_max: 300

##  Uncomment for 350mm build
#position_endstop: 350
#position_max: 350

##--------------------------------------------------------------------
homing_speed: 80  #Max 100
homing_retract_dist: 5
homing_positive_dir: true

##  Make sure to update below for your relevant driver (2208 or 2209)
#[tmc2209 stepper_y]
#uart_pin: PD11
#interpolate: false
#run_current: 0.8
#sense_resistor: 0.110
#stealthchop_threshold: 0
[tmc5160 stepper_y]
cs_pin: PD11
run_current: 0.800
hold_current: 0.500
stealthchop_threshold: 0
spi_software_mosi_pin: PA7
spi_software_miso_pin: PA6
spi_software_sclk_pin: PA5

#####################################################################
#   Z Stepper Settings
#####################################################################

## Z0 Stepper - Front Left
##  Connected to MOTOR_2
##  Endstop connected to DIAG_2



[stepper_z3]
step_pin: PF11
dir_pin: PG3
enable_pin: !PG5
rotation_distance: 40
gear_ratio: 80:20
microsteps: 32


##  Make sure to update below for your relevant driver (2208 or 2209)
[tmc2209 stepper_z3]
uart_pin: PC6
interpolate: false
run_current: 0.8
sense_resistor: 0.110
stealthchop_threshold: 10000

##  Z1 Stepper - Rear Left
##  Connected to MOTOR_3
[stepper_z]
step_pin: PG4
dir_pin: !PC1
enable_pin: !PA0
rotation_distance: 40
gear_ratio: 80:20
microsteps: 32
endstop_pin: probe:z_virtual_endstop 
#endstop_pin: PG10
##  Z-position of nozzle (in mm) to z-endstop trigger point relative to print surface (Z0)
##  (+) value = endstop above Z0, (-) value = endstop below
##  Increasing position_endstop brings nozzle closer to the bed
##  After you run Z_ENDSTOP_CALIBRATE, position_endstop will be stored at the very end of your config
#position_endstop: -0.5
##--------------------------------------------------------------------

##  Uncomment below for 250mm build
position_max: 230

##  Uncomment below for 300mm build
#position_max: 280

##  Uncomment below for 350mm build
#position_max: 330

##--------------------------------------------------------------------
position_min: -5
homing_speed: 8
second_homing_speed: 3
homing_retract_dist: 3


##  Make sure to update below for your relevant driver (2208 or 2209)
[tmc2209 stepper_z]
uart_pin: PC7
interpolate: false
run_current: 0.8
sense_resistor: 0.110
stealthchop_threshold: 10000


##  Z2 Stepper - Rear Right
##  Connected to MOTOR_4
[stepper_z2]
step_pin: PF9
dir_pin: !PF10
enable_pin: !PG2
rotation_distance: 40
gear_ratio: 80:20
microsteps: 32

##  Make sure to update below for your relevant driver (2208 or 2209)
[tmc2209 stepper_z2]
uart_pin: PF2
interpolate: false
run_current: 0.8
sense_resistor: 0.110
stealthchop_threshold: 10000

##  Z3 Stepper - Front Right
##  Connected to MOTOR_5
[stepper_z1]
step_pin: PC13
dir_pin: PF0
enable_pin: !PF1
rotation_distance: 40
gear_ratio: 80:20
microsteps: 32

##  Make sure to update below for your relevant driver (2208 or 2209)
[tmc2209 stepper_z1]
uart_pin: PE4
interpolate: false
run_current: 0.8
sense_resistor: 0.110
stealthchop_threshold: 10000


#####################################################################
#   Extruder
#####################################################################

##  Connected to MOTOR_6
##  Heater - HE0
##  Thermistor - T0
[extruder]
step_pin: PE2
dir_pin: PE3
enable_pin: !PD4
##  Update value below when you perform extruder calibration
##  If you ask for 100mm of filament, but in reality it is 98mm:
##  rotation_distance = <previous_rotation_distance> * <actual_extrude_distance> / 100
##  22.6789511 is a good starting point
#rotation_distance: 34.406 ;MK8
rotation_distance: 22.6789511   #Bondtech 5mm Drive Gears
##  Update Gear Ratio depending on your Extruder Type
##  Use 50:10 for Stealthburner/Clockwork 2
##  Use 50:17 for Afterburner/Clockwork (BMG Gear Ratio)
##  Use 80:20 for M4, M3.1
gear_ratio: 50:10               #BMG Gear Ratio
microsteps: 32
full_steps_per_rotation: 200    #200 for 1.8 degree, 400 for 0.9 degree

max_extrude_only_distance: 2000.0
#max_extrude_only_velocity: 50
#max_extrude_only_accel: 2500
#instantaneous_corner_velocity: 1.500
#max_extrude_cross_section: 50
pressure_advance: 0.0304

nozzle_diameter: 0.400
filament_diameter: 1.75
heater_pin: PB11
##  Validate the following thermistor type to make sure it is correct
##  See https://www.klipper3d.org/Config_Reference.html#common-thermistors for additional options
#sensor_type: ATC Semitec 104GT-2
sensor_type: EPCOS 100K B57560G104F
sensor_pin: PF4
min_temp: -5
max_temp: 270
max_power: 1.0
min_extrude_temp: 10
control = pid
pid_Kp=34.612 
pid_Ki=11.537 
pid_Kd=25.959
##  Try to keep pressure_advance below 1.0
#pressure_advance: 0.05
##  Default is 0.040, leave stock
#pressure_advance_smooth_time: 0.040
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

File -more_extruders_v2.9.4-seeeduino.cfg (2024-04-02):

#匹配换色gcodev2.2

########################################
############### 换色配置 ################
#[四色滑槽选择]、[无外部判断方案方案2-逻辑2]、[全手动挤出机配置]、[分离送料和加载料流程]、[分步换色修改为一键换色]、[调整配置逻辑 分离hardware software]、[一键装卸耗材]、[开启开机确认宏]
#[缓存高低限位，耗材加载时触发高限位立即停]-230722、[添加从Ta直接切换到Tb]、[分离耗材回抽前冲击-0923]、[添加缓冲器开关-1029bug]
########################################

# 外部配置文件引入
[include MCU1_seeeduino_rename_pins.cfg]#feiw 引入兔子主板的重映射pin
#[include mz_motorrewind.cfg]
#[include rewind.cfg]
########################################
# 变量
########################################
# params变量 #
# params.TEMPERATURE ##切片Gcode添加 temperature=[nozzle_temperature]

[gcode_macro COLORS_VAR]
description: 保存换色相关变量的空宏
variable_huichou: 125           #feiw 切换宏中的回抽长度参数值【耗材融化处到送料管出口出的长度，该数据为测量挤出头到近程挤出机送料齿轮的长度。数据为参考值，初始设置建议偏大5mm-10mm，但不可小于测量值】
variable_safe0: 50               #feiw 切换宏中的回抽和退料长度衔接点后移参数值(挤出机和手动送料步进电机协同工作长度的额外增量)【用于耗材丝离开挤出机后仍有一段与送料电机协作过程，作为退料的安全量】
variable_jinliao: 125            #feiw 切换宏中的加载耗材时前进长度的参数值【耗材离开送料管进入挤出机后前进长度】
variable_safe1: 35               #feiw 切换宏中的加载和送料长度衔接点后移参数值(挤出机和手动送料步进电机协同工作长度的额外增量)【用于耗材丝进入挤出机时提前与送料电机协作工作，作为进料的安全量】
variable_songsi02: 175         #feiw 切换宏中的耗材预备位置(4in1开始处)到远程送料口出口的长度
variable_songsi13: 175    #feiw 耗材从储备位移动到目标位置长度（由于安装问题，“0,2”耗材和“1,3”耗材到达目标位置需要挤出长度不同
variable_bowdenspeed: 9500      #feiw 切换宏中的送料管阶段速度，以F单位格式[F:毫米/每分钟]
variable_jiazaispeed: 360        #feiw 切换进料宏中的远近双挤出协同进入加热块阶段速度，以F单位格式
## 同步段挤出速度最好低于预设 （F300 5mm/s 6.01mm³/s）（F360 6mm/s 7.21mm³/s） （F420 7mm/s 8.41mm³/s）（F480 8mm/s 9.62mm³/s）（F540 9mm/s 10.82mm³/s）
# 下列：回抽前挤出相关
variable_ramming_in: 35         #feiw 切换退料宏中的“抽离前”挤出阶段长度（mm）
variable_ramming_out: 125         #feiw 切换退料宏中的“抽离时”高速回抽阶段长度（mm）
variable_rammingspeed: 3000      #feiw 切换退料宏中的“抽离时”高速回抽阶段速度，以F单位格式

#下列：停靠坞相关
variable_xm6: 40                 #feiw change_dock中停靠X坐标
variable_ym6: 305                #feiw change_dock中停靠Y坐标
variable_nozzlex: 150            #feiw 换色耗材挤出后断开路过擦嘴点后的停靠坐标（本机change_dock坐标的x方向为擦嘴，定义该坐标后机器每次换料结束经过擦嘴断开冲洗耗材）

#下列：温度判定相关
variable_min_temp: 180           #feiw 低于该温度不加热
variable_default_temp: 270       #feiw 默认加热的温度

#下列：缓冲器启用【未启用缓冲时注销[filament_switch_sensor buffer_sensor_H]、[filament_switch_sensor buffer_sensor_L]两项及[duplicate_pin_override]中对应的限位开关复用点位】
variable_buffer_switch: 1        #feiw 值为1启用缓冲器
#下列：自动续料相关【未启用】
variable_change_number: 0        #feiw 自动换色次数

#变量数组的创建【不要改】
variable_colorselector = [180, 0, -90, 90] #对应四色模块的旋转值
variable_now_filament: 0         #feiw 当前加载的耗材色号，通过【SET_GCODE_VARIABLE MACRO=<macro_name> VARIABLE=<name> VALUE=<value>】修改，例:SET_GCODE_VARIABLE MACRO=COLORS_VAR VARIABLE=Thaoma VALUE=1
#variable_colorserial = [0, 1, 2, 3]        #对应四色模块的耗材色号【暂时没想好】

gcode:

# variable_colorselector = [2.4, 24.0, 44.8, 71.2, 92.0, 113.6, 139.2, 160.8, 181.6] #变量数组的创建
# {printer["gcode_macro _ERCF_VAR"].colorselector[params.TOOL|int]}                  #变量数组的调用


########################################
# 换色前后准备宏（暂定打印 可能切料 移动到指定区域 ）
########################################
# SET_FILAMENT_SENSOR SENSOR=encoder_sensor ENABLE=0 设置耗材检测停用
# MANUAL_STEPPER STEPPER=filament_motion SET_POSITION=0 SPEED=35 ACCEL=6000 MOVE={huichou+safe0} SYNC=0
## 将耗材手动步进电机和挤出机同步匹配 (设置当前位置为0坐标、速度为35mm/s（等效F2100）、加速度为移动{huichou}长度、允许和后面的Gcode同步执行) 
## 【添加“SYNC=0”后，下一行需要存在G代码方可执行（执行下一行的G代码时同步运行）】

[gcode_macro change_out]   #feiw 耗材切换前处理
description: 耗材切换处理-卸载耗材
gcode:
  {% set COLORS_VAR = printer["gcode_macro COLORS_VAR"] %}
  {% set huichou = COLORS_VAR.huichou|int %}               # 设置变量“高速回抽长度”
  {% set safe0 = COLORS_VAR.safe0|int %}                   # 设置变量“回抽长度和退料长度衔接点后移”
  {% set songsi02 = COLORS_VAR.songsi02|int %}             # 设置变量“T0,T2送丝长度”
  {% set songsi13 = COLORS_VAR.songsi13|int %}             # 设置变量“T1,T3送丝长度”
  {% set bowdenspeed = COLORS_VAR.bowdenspeed|int %}       # 设置变量“管内速度”
  {% set min_temp = COLORS_VAR.min_temp|int %}             # 设置变量“最低挤出温度判定”
  {% set default_temp = COLORS_VAR.default_temp|int %}     # 设置变量“低于最低挤出温度后设定默认温度”
  {% set rammingspeed = COLORS_VAR.rammingspeed|int %}     # 设置变量“冲击-脱离加热块速度”
  {% set ramming_in = COLORS_VAR.ramming_in|int %}         # 设置变量“冲击-脱离加热块前长度”
  {% set ramming_out = COLORS_VAR.ramming_out|int %}       # 设置变量“冲击-脱离加热块过程长度”
  {% set Current_T = params.T_FILAMENT|float %}            # T_FILAMENT=(0,1,2,3) 引用虚拟外部变量(指定耗材号)

  SAVE_GCODE_STATE     # 保存当前g代码坐标解析状态，便于进行Gcode编辑后恢复状态
  CUT
  #切料在这里之前
  {% if printer.extruder.temperature < min_temp %}     #feiw 如果当前挤出机温度不够 加热挤出机到默认温度
    M109 S{default_temp}
  {% else %}
    M104 S{printer.extruder.temperature}               #feiw 保持温度不变
  {% endif %}

  #G91                                                  # 设置相对坐标模式(G91)
  G90
  M83                                                  # 挤出机使用相对定位
  {% if Current_T == 0 or Current_T == 2 %}
  #feiw 【对于T0,T2耗材，回抽方向顺时针】
    # 回抽前挤出料，用于挤出喉管内变形耗材  F:毫米/每分钟
    MANUAL_STEPPER STEPPER=filament_motion SET_POSITION=0 SPEED={600/60} ACCEL=5000 MOVE=-{ramming_in} SYNC=0
    G1 E{ramming_in} F600                              # F:毫米/每分钟 【手动步进电机的速度单位为mm/s,与G1指令的F命令不同】
    # 回抽退料，用于快速离开热端  F:毫米/每分钟 
    MANUAL_STEPPER STEPPER=filament_motion SET_POSITION=0 SPEED={rammingspeed/60} ACCEL=5000 MOVE={ramming_out} SYNC=0 # 将耗材手动步进电机和挤出机同步（设置相同的参数）。速度单位不同：45mm/s（等效F2700）
    G1 E-{ramming_out} F{rammingspeed}                             # F:毫米/每分钟 【手动步进电机的速度单位为mm/s,与G1指令的F命令不同】
    M400                                               # 等待当前所有移动指令完成
    # 回抽退料，用于慢速离开挤出机  F:毫米/每分钟
    MANUAL_STEPPER STEPPER=filament_motion SET_POSITION=0 SPEED={1800/60} ACCEL=5000 MOVE={huichou+safe0-ramming_out} SYNC=0
    G1 E-{huichou+safe0-ramming_out} F1800
    M400
    #G4 P2000                                          # 驻留：G4 P<毫秒> 【调试阶段用】
    # 送料管退料
    MANUAL_STEPPER STEPPER=filament_motion SET_POSITION=0 SPEED={bowdenspeed/60} ACCEL=3000 MOVE={songsi02-safe0}
  #{% else %}
  {% elif Current_T == 1 or Current_T == 3 %}
  #feiw 【对于T1,T3耗材，回抽方向逆时针】
    # 回抽前挤出料，用于挤出喉管内变形耗材  F:毫米/每分钟
    MANUAL_STEPPER STEPPER=filament_motion SET_POSITION=0 SPEED={600/60} ACCEL=5000 MOVE={ramming_in} SYNC=0
    G1 E{ramming_in} F600
    # 回抽退料，用于快速离开热端  F:毫米/每分钟
    MANUAL_STEPPER STEPPER=filament_motion SET_POSITION=0 SPEED={rammingspeed/60} ACCEL=5000 MOVE=-{ramming_out} SYNC=0
    G1 E-{ramming_out} F{rammingspeed}
    M400                                               # 等待当前所有移动指令完成
    # 回抽退料，用于慢速离开挤出机  F:毫米/每分钟
    MANUAL_STEPPER STEPPER=filament_motion SET_POSITION=0 SPEED={1800/60} ACCEL=5000 MOVE=-{huichou+safe0-ramming_out} SYNC=0
    G1 E-{huichou+safe0-ramming_out} F1800
    M400
    #G4 P2000                                          # 驻留：G4 P<毫秒> 【调试阶段用】
    #送料管退料
    MANUAL_STEPPER STEPPER=filament_motion SET_POSITION=0 SPEED={bowdenspeed/60} ACCEL=3000 MOVE=-{songsi13-safe0}
  {% endif %}
  RESTORE_GCODE_STATE   # 恢复当前g代码坐标解析状态 如果指定“MOVE=1”，则将发出刀头移动以返回到先前的 XYZ 位置。如果指定了“MOVE_SPEED”，则刀头移动将以给定速度（以毫米/秒为单位）执行；否则工具头移动将使用恢复的 g 代码速度。
[gcode_macro change_in]   #feiw 耗材切换后处理
description: 耗材切换处理-加载耗材
gcode:
  {% set COLORS_VAR = printer["gcode_macro COLORS_VAR"] %}
  {% set jinliao = COLORS_VAR.jinliao|int %}               # 设置变量“新耗材加载前进长度”
  {% set safe1 = COLORS_VAR.safe1|int %}                   # 设置变量“进料长度和送料长度衔接点后移”
  {% set songsi02 = COLORS_VAR.songsi02|int %}             # 设置变量“T0,T2送丝长度”
  {% set songsi13 = COLORS_VAR.songsi13|int %}             # 设置变量“T1,T3送丝长度”
  {% set bowdenspeed = COLORS_VAR.bowdenspeed|int %}       # 设置变量“管内速度”
  {% set jiazaispeed = COLORS_VAR.jiazaispeed|int %}       # 设置变量“双挤出同步段进料速度”
  {% set buffer_switch = COLORS_VAR.buffer_switch|int %}   # 设置变量“缓冲器的启用”
  {% set min_temp = COLORS_VAR.min_temp|int %}             # 设置变量“最低挤出温度判定”
  {% set default_temp = COLORS_VAR.default_temp|int %}     # 设置变量“低于最低挤出温度后设定默认温度”
  # 设置旧温度为宏反馈温度（如果想要用“params.TEMPERATURE”获取温度，要在切片的开始Gcode中添加“temperature=[nozzle_temperature]”）（“printer.extruder.temperature”为当前热端温度）
  {% set Current_T = params.T_FILAMENT|float %}        # T_FILAMENT=(0,1,2,3) 引用虚拟外部变量(指定耗材号)

  SAVE_GCODE_STATE                                     # 保存当前g代码坐标解析状态，便于进行Gcode编辑后恢复状态
  {% if printer.extruder.temperature < min_temp %}     #feiw 如果当前挤出机温度不够 加热挤出机到默认温度
    M109 S{default_temp}
  {% else %}
    M104 S{printer.extruder.temperature}               #feiw 保持温度不变
  {% endif %}
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

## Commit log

2023-01-05 Update printer.cfg
    filament motion detect added
    Mesh added
    [printer.cfg]
2023-03-16 backup for cr10 hotend
    [printer.cfg]
2023-03-29 Update printer.cfg
    1
    [printer.cfg]
2023-03-31 filament_buffer added
    [filament_buffer.dwg]
2023-06-05 Dual Color cfg added
    [DualColor_printer.cfg]
2023-06-15 added chinese text for Dualcolor
    [DualColor_printer.cfg, printer-creality-sermoonD1-2021.cfg]
2024-02-01 Organize files
    [2.4-bigtreetech-octopus.cfg, BTT_OctoPus_Voron2_Config.cfg, Filament_Switch_Sensor.cfg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]
2024-02-01 Create fix knife Miu version BOM.png
    spring added
2024-02-01 added G4 p200 for jingliao marco
    [MZ_Ams_lite.cfg]
2024-02-05 new macro added for filament runout
    [Filament_Switch_Sensor.cfg, MZ_Ams_lite.cfg, Var.cfg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]
2024-03-01 Update buffer.cfg
    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
    [buffer.cfg]
2024-03-07 continue marco added
    [Filament_Switch_Sensor.cfg]
2024-03-16 update all
    [Filament_Continue.cfg, Lite_haredware.cfg, MZ_Ams_lite.cfg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]
2024-03-16 sw add
    [Filament_Continue.cfg, Filament_buffer.cfg, Lite_haredware.cfg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]
2024-11-12 muzi_v2 added
    [-more_extruders_v2.9.3-seeeduino.cfg, -more_extruders_v2.9.4-seeeduino.cfg, Auto_shutdown.cfg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]
